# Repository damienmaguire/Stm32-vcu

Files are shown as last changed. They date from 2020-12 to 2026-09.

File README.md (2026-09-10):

# stm32-vcu (ZombieVerter VCU)

Build status

Project based on the OpenInverter System by Johannes Huebner to provide a universal VCU (Vehicle Control Unit) for electric vehicle conversion projects. 

Please visit the development thread on the Openinverter Forum for more information : https://openinverter.org/forum/viewtopic.php?f=3&t=1277
Zom_V1_3

V1.3 Hardware now released. PDFs and Gerber here on Github, full Kicad 9 design is on Patreon at the 10Eur level.

## Required Bootloader

STM32-Serial https://github.com/jsphuebner/tumanako-inverter-fw-bootloader/releases/tag/v5.2

STM32-CAN https://github.com/jsphuebner/stm32-CANBootloader

## Videos on progress

Project introduction : https://vimeo.com/506480876

V1.11a On dyno with GS450h / BMW E39 : https://vimeo.com/802405172

V2.00a now available : https://vimeo.com/824494783?share=copy

V2.15a now available : https://www.youtube.com/watch?v=iwB3wxCEFo0

V2.20A now available : https://www.youtube.com/watch?v=wjlucUWX_lc

V2.40A now available : https://vimeo.com/1201141543?fl=ip&fe=ec

# Supported components

- Nissan Leaf Gen1/2/3 inverter via CAN
- Nissan Leaf Gen1/2/3 PDM (Charger and DCDC)
- Nissan LEAF Battery (all variants)
- Mitsubishi Outlander Support
- Mitsubishi Outlander drivetrain (front and rear motors/inverters) Support
- Modular BMS / SimpBMS Support
- OpenInverter CAN Support
- CCS DC fast charge via BMW i3 LIM
- CCS DC fast charging via FOCCCI https://github.com/uhi22/ccs32clara
- Chademo DC fast charge
- ISA Shunt / BMW SBOX / VW EBOX supported via CAN
- Lexus GS450H inverter / gearbox via sync serial
- Lexus GS300H inverter / gearbox via sync serial
- Toyota Prius/Yaris/Auris Gen 3 inverters via sync serial
- BMW E46 CAN support
- BMW E39 CAN support
- BMW E65 CAN Support
- BMW E31 CAN Support
- Mid 2000s VAG Can support
- Subaru vehicle support
- Opel Ampera / Chevy Volt 6.5kw cabin heater
- VW LIN based 6.5kw cabin heater
- Elcon charger Support
- OBD2 Can support
- TESLA Gen 2 DCDC Converter Can support

# Contributing

Information on how to contribute to this open source project can be found [Contributing Guide](./CONTRIBUTING.md)

# Compiling
You will need the arm-none-eabi toolchain: https://developer.arm.com/open-source/gnu-toolchain/gnu-rm/downloads
On Linux this can be installed by typing:

`sudo apt install gcc-arm-none-eabi`

The only external depedencies are libopencm3 and libopeninv. You can download and build this dependency by typing

`make get-deps`

Now you can compile stm32-vcu by typing

`make`

# Tests

Build the tests

`make Tests`

Run the tests

`./test/test_vcu`

And upload it to your board using a JTAG/SWD adapter, the updater.py script or the esp8266 web interface

I use CodeBlocks IDE :  https://www.codeblocks.org/

Sept 21 : V1 hardware and firmware from "Master" branch now running in my E46 Touring and E39 vehicles.

March 24 : V1.1 Hardware and V2.05A firmware now running in 3 vehicles :

-BMW E39 with Lexus GS450H Drivetrain, Tesla PCS, ISA Shunt , Chademo Fast Charge

-BMW E46 Touring with Nissan Leaf Gen 1 Drivetrain, Outlander Charger / DCDC, ISA Shunt , CCS Fast Charge

-BMW E31 with Tesla LDU Drivetrain, Tesla DCDC, ISA Shunt , Chademo Fast Charge

All hardware / software is tested in these vehicles before release. More vehicles with different configuration in progress to ensure as much testing as possible.

Apr 26 : Added Zombie Relay box V1 full kicad project to hardware directory.

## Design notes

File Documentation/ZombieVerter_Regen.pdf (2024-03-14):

ZombieVerter Regen
14/03/2024
Tom dB
Pull request https://github.com/damienmaguire/Stm32-vcu/pull/78 implements regen and introduces new parameters. This document explains the new parameters.

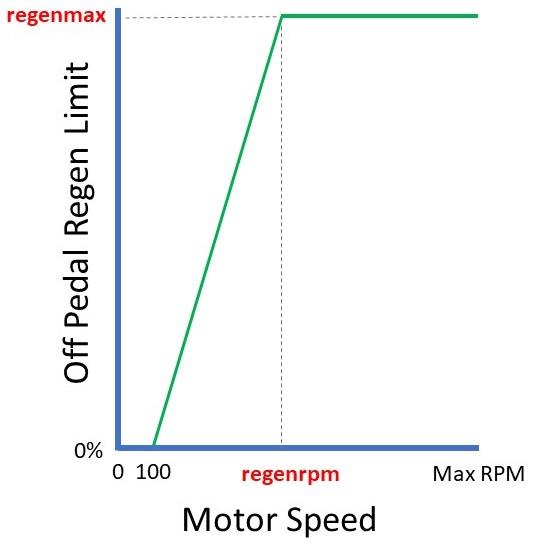
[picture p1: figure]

Regenrpm – The motor rpm at which regenmax is used as the regen limit. Under this rpm the regen limit is tapered to 0% at 100 rpm. This is applied to both Regenmax and regenBrak. Regenmax – The maximum allow regen in potnom percentage, always negative or 0. Ramps down based on motor rpm.

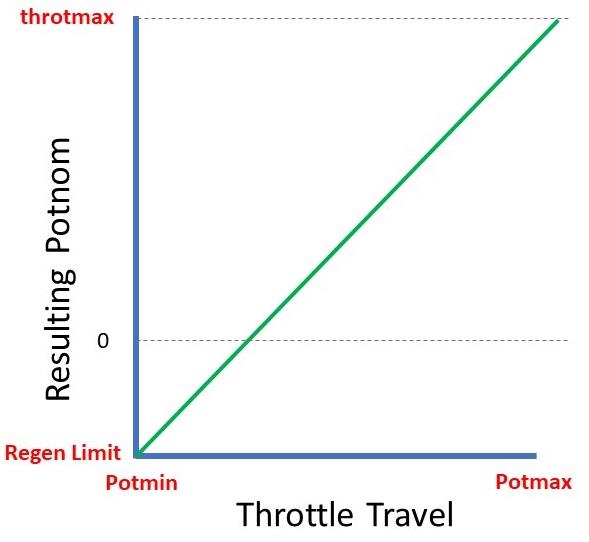
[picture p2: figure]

throtmax – Maximum allow positve potnom request in the forward direction.

throtmaxRev – Maximum allow positive potnom request in the reverse direction. Throtmin – Minimum (most negative) allowed potnom at all times.
Throtramp – The amount of allowed potnom change per %/10ms. Throtramprpm- Above this motor rpm Throtramp is no longer applied.

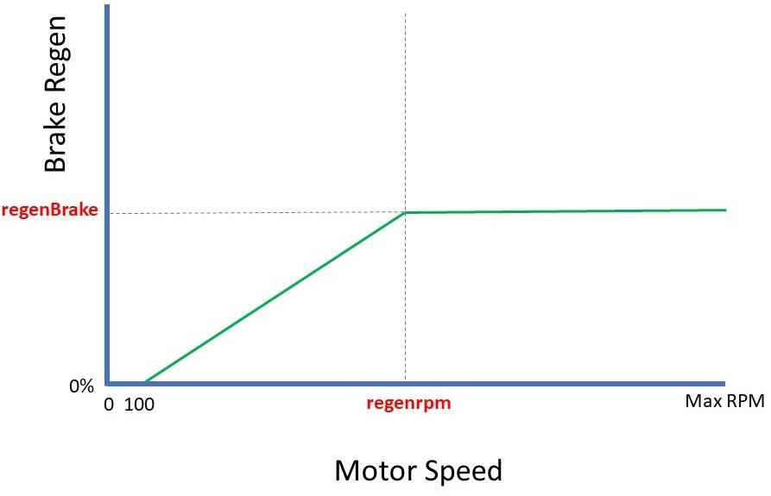
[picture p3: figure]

regenBrake – Brake pedal based negative potnom request, always negative or 0. Ramps down based on motor rpm.

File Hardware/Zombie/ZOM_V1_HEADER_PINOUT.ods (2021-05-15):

ZombieVerter VCU V1 cable side pinout.
Note: pins are referenced from the REAR of the plug.
Pin Number | Wire Colour | Function | Comment
1 | green | RS232 Rx | Rs232 comms from Usart 3 on mcu. May be used for remote wifi locating or direct serial terminal comms.
2 | purple | RS232 Tx | Rs232 comms from Usart 3 on mcu. May be used for remote wifi locating or direct serial terminal comms.
3 | white | GP Out 3 | General purpose protected Low side switched output from PD13
4 | blue | GP Out 2 | General purpose protected Low side switched output from PD14
5 | purple | PWM 3 | General purpose pwm output. Push/pull driven to +12v/gnd. Timer 3 Chan 3 PB0.
6 | orange | PWM 2 | General purpose pwm output. Push/pull driven to +12v/gnd. Timer 3 Chan 2 PA7.
7 | orange | PWM 1 | General purpose pwm output. Push/pull driven to +12v/gnd. Timer 3 Chan 1 PA6.
8 | orange | Analog 2 in | General purpose analog input 0-5v.PC3.
9 | orange | Analog 1 in | General purpose analog input 0-5v.PC2.
10 | orange | DAC 2 | Digital to Analog converter output 1. Amplified via TDA2822 to max 12v level. PA5.
11 | brown | DAC 1 | Digital to Analog converter output 1. Amplified via TDA2822 to max 12v level. PA4.
12 | blue | MG2 Temp - | Motor 2 temp sensor. Can be used for Toyota hybrid transmissions or as a general purpose motor temp input.PC4.
13 | yellow | MG2 Temp + | Motor 2 temp sensor. Can be used for Toyota hybrid transmissions or as a general purpose motor temp input.PC4.
14 | green | MG1 Temp - | Motor 2 temp sensor. Can be used for Toyota hybrid transmissions or as a general purpose motor temp input.PC5.
15 | purple | Ignition T15 In | Terminal 15 ignition on 12v input. Tells the vcu the key is in the on position.PD6.
16 | purple | REQ- | Toyota Hybrid inverter serial comms.PE6.
17 | yellow | REQ+ | Toyota Hybrid inverter serial comms.PE6.
18 | yellow | CLK- | Toyota Hybrid inverter serial comms clock. Timer 2 Channel 2. PA1.
19 | green | CLK+ | Toyota Hybrid inverter serial comms clock. Timer 2 Channel 2. PA1.
20 | green | MTH- | Toyota Hybrid inverter serial comms.Usart 2.
21 | brown | MTH+ | Toyota Hybrid inverter serial comms.Usart 2.
22 | brown | HTM- | Toyota Hybrid inverter serial comms.Usart 2.
23 | white | HTM+ | Toyota Hybrid inverter serial comms.Usart 2.
24 | green | LIN | Local interconnect network. Usart 1.
25 | blue | CAN EXT 3L | CAN 3 interface. Choice of HS/SW/FT modes via jumpers.
26 | yellow | CAN EXT 3H | CAN 3 interface. Choice of HS/SW/FT modes via jumpers.
27 | red | CAN EXT 2L | CAN 2 interface. HS only. Terminated with 120R by default.
28 | red | CAN EXT 2H | CAN 2 interface. HS only.
29 | white | MG1 Temp + | Motor 2 temp sensor. Can be used for Toyota hybrid transmissions or as a general purpose motor temp input.PC5.
30 | brown | Oil Pump PWM | PWM for Toyota hybrid oil pump speed control. Weak pullup to +12v via 1k. May be used as a general low power low side pwm output. Timer 1 channel 1 PE9.
31 | brown | GP Out 1 | General purpose protected Low side switched output from PD15.
32 | green | Inverter Power | Low side switched output for controlling drive inverter power relay.PA8.
33 | yellow | Main Contactor | Low side switched output for controlling main HV contactor.PC7.
34 | blue | Precharge | Low side switched output for controlling main HV precharge contactor.PC6.
35 | black | Pot 2 | Output from AD5160 0-5k digital potentiometer. Controlled via SPI3.
36 | purple | Pot 1 | Output from AD5160 0-5k digital potentiometer. Controlled via SPI3.
37 | green | Trans SP | Protected high side switched +12v supply to Toyota hybrid transmission. May be used as a GP output if desired.PD12.
38 | blue | Trans SL2- | Protected low side switched +12v supply to Toyota hybrid transmission. May be used as a GP output if desired.PC8.
39 | yellow | Trans SL1- | Protected low side switched +12v supply to Toyota hybrid transmission. May be used as a GP output if desired.PC9.
40 | green | Trans PB3 | Input from Toyota hybrid transmission gear position indicator. May be used as a GP input if desired.PE5.
41 | red | Trans PB2 | Input from Toyota hybrid transmission gear position indicator. May be used as a GP input if desired.PE4.
42 | black | Trans PB1 | Input from Toyota hybrid transmission gear position indicator. May be used as a GP input if desired.PE3.
43 | black | CAN EXT L | CAN 1 interface. HS only. Terminated with 120R by default.
44 | black | CAN EXT H | CAN 1 interface. HS only.
45 | black | Throttle Ground | Hall effect throttle pedal/position sensor ground.
46 | black | Throttle 2 | Hall effect throttle pedal/position sensor channel 2. PC1.
47 | black | Throttle 1 | Hall effect throttle pedal/position sensor channel 1. PC0.
48 | black | +5v Throttle | Hall effect throttle pedal/position sensor +5v supply.
49 | black | Brake input | Brake light switch input.PA15.
50 | orange | GP12v Input | General purpose 12v digital input.PD4.
51 | 2 core brown | Hvrequest | High voltage switch on/off request digital 12v input. Typically used by a charger to request HV activation.PD5.
52 | 2 core blue | Start | Start signal momentary digital 12v input. Typically connected to the start position of a traditional ignition switch.
53 | 2 core brown | Reverse Direction | Pull to +12v for reverse direction
54 | 2 core blue | Forward Direction | Pull to +12v for forward direction
55 | Purple | Ground | Connect to vehicle chassis ground
56 | Green | Permanent +12V | Connect to permanent +12v via 5amp fuse
Notes :
Yellow highlighted connections are unrouted in pre release hardware.
Workaround : Use GP analog i/p for temp and gp 12v input for brake light.
Will be corrected in release hardware.

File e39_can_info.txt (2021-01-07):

void SendBMW()
{
uint16_t outRPM = (GetInt(Param::speed)*7);
uint16_t tempValue = (GetInt(Param::tmphs)*4);
if(outRPM<4800) outRPM=4800;  //set lowest rpm to 750 displayed on tach to keep car alive thinking engine is running.
if(outRPM>44800) outRPM=44800;  //DONT READ MORE THAN 7000RPM!

 char outRPMlo = outRPM & 0xFF;
 char outRPMhi = outRPM >> 8;

char ABSMsg;
bmw dme1Data;
dme1Data.bytes[0] = 0x05;
dme1Data.bytes[1] = 0x00;
dme1Data.bytes[2] = outRPMlo;  //RPM LSB
dme1Data.bytes[3] = outRPMhi;  //RPM MSB [RPM=(hex2dec("byte3"&"byte2"))/6.4]  0x12c0 should be 750rpm on tach
dme1Data.bytes[4] = 0x00;
dme1Data.bytes[5] = 0x00;
dme1Data.bytes[6] = 0x00;
dme1Data.bytes[7] = 0x00;

    if(counter_329 >= 22) counter_329 = 0;
    if(counter_329==0) ABSMsg=0x11;
    if(counter_329>=8 && counter_329<15) ABSMsg=0x86;
    if(counter_329>=15) ABSMsg=0xd9;
    counter_329++;

bmw dme2Data;
dme2Data.bytes[0] = ABSMsg;  //needs to cycle 11,86,d9
dme2Data.bytes[1] = tempValue; //temp bit tdata
dme2Data.bytes[2] = 0xc5;
dme2Data.bytes[3] = 0x00;
dme2Data.bytes[4] = 0x00;
dme2Data.bytes[5] = 0x00; //Throttle position currently just fixed value
dme2Data.bytes[6] = 0x00;
dme2Data.bytes[7] = 0x00;

bmw dme3Data;
dme3Data.bytes[0] = 0x00;  //2=check ewwngine on , 0=check engine off
dme3Data.bytes[1] = 0x00; //LSB fuel comp
dme3Data.bytes[2] = 0x00;  //MSB fuel comp
dme3Data.bytes[3] = 0x00;   // hex 08 = Overheat light on
dme3Data.bytes[4] = 0x7E;
dme3Data.bytes[5] = 0x10;
dme3Data.bytes[6] = 0x00;
dme3Data.bytes[7] = 0x18;

 uint32_t dataBMW316[2] = {dme1Data.value[0],dme1Data.value[1] };
 uint32_t dataBMW329[2] = {dme2Data.value[0],dme2Data.value[1] };
 uint32_t dataBMW545[2] = {dme3Data.value[0],dme3Data.value[1]};

Send(0x316,dataBMW316);
Send(0x329,dataBMW329);
Send(0x545,dataBMW545);

}

 void SendBMW();

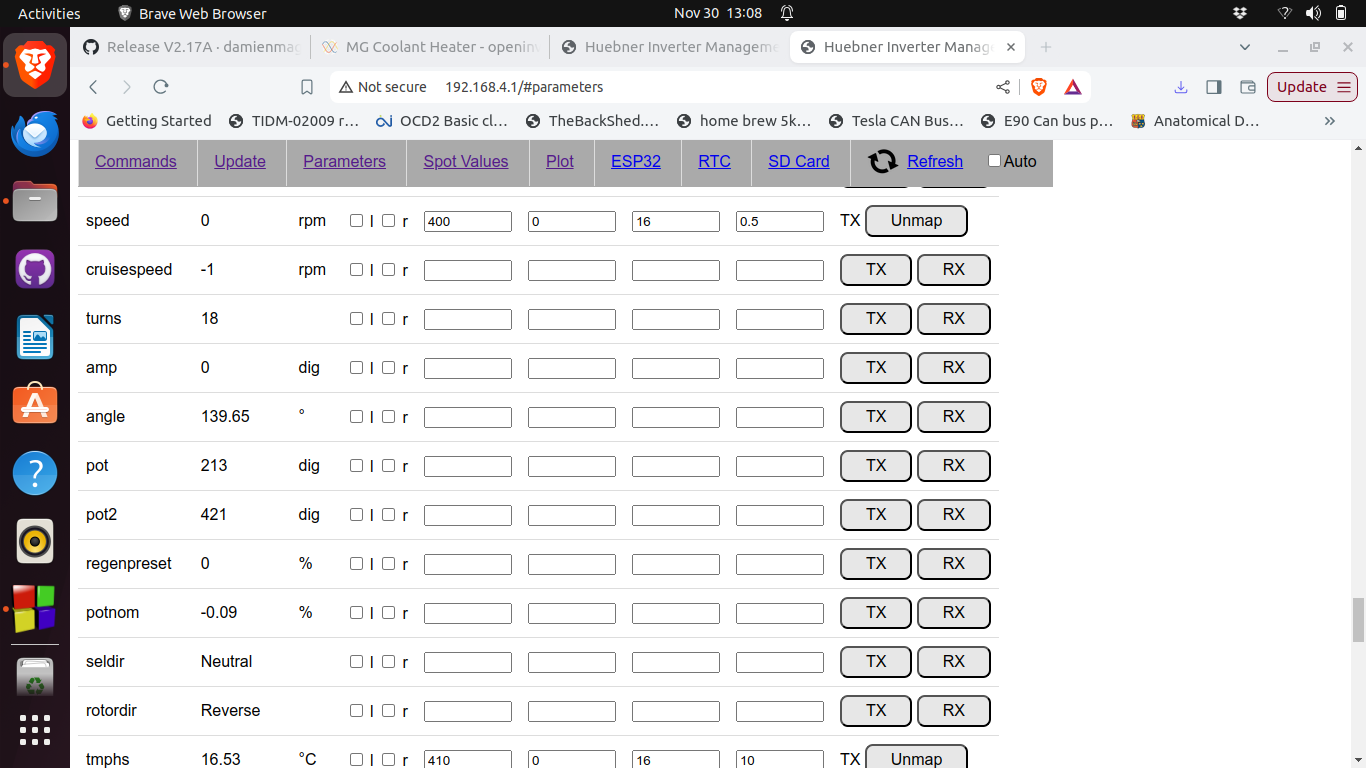
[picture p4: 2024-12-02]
Parameters/Screenshot from 2024-11-30 13-08-50.png

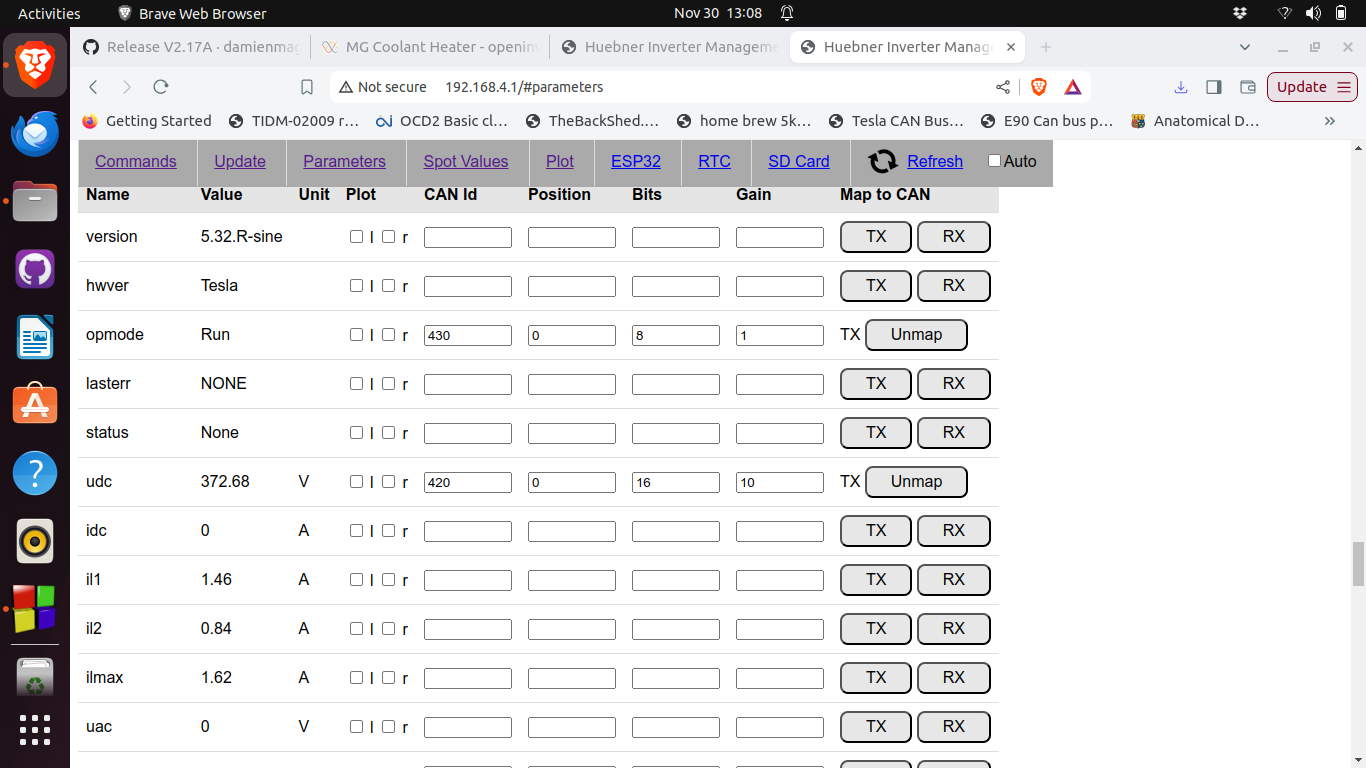
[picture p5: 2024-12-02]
Parameters/Screenshot from 2024-11-30 13-08-35.png

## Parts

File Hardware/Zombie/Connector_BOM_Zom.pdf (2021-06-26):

## ZombieVerter VCU Connector List :

### Header, Enclosure and Connector:

https://www.aliexpress.com/item/32857771975.html?spm=a2g0s.9042311.0.0.39f24c4dWOmGPE

### Wiring Harness:

https://www.aliexpress.com/item/4001213569338.html?spm=a2g0o.cart.0.0.366c3c00qhBvGO&mp=1

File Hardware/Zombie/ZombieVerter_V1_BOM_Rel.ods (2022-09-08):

Comment | Designator | Footprint
1N4148WS | D2,D3,D6,D4,D7,D8,D9,D10,D11 | SOD-323F
100uF | C17,C21 | C1206
AD5160BRJZ10-RL7 | IC21,IC22 | SOT-23-8
AMS117-3.3V | IC4
0.1uF | C4,C16,C40,C55,C34,C32,C27,C19,C43,C62,C37,C50,C51,C53,C56,C73,C74,C26,C24,C18,C28,C12,C9,C36,C41,C42 | 0805_C
0.47uF | C57,C58,C59 | 0805_C
1uF | C8,C30,C3,C2,C39,C7,C6,C5,C33,C31,C15,C44,C46,C47,C60,C61,C63,C66,C67,C70,C71,C72,C22,C14,C48,C38,C54 | 0805_C
3n3 | C45 | 0805_C
10nF | C68 | 0805_C
22pF | C10,C11 | 0805_C
100pF | C64,C65 | 0805_C
10uF | C35,C1,C49,C52,C25 | 0805_C
DLP11SA900HL2L | L4,L5 | SMD-4_1.0x1.3x0.55P
FAN3122TMX | IC27,IC28,IC29 | SOIC-8_3.9x4.9x1.27P
RED LED | LED1,LED2 | LED_0805
M24M02/M2401 | IC2 | SOIC-8_3.9x4.9x1.27P
MAX3221ECPWR | IC30 | HTSSOP-16_EP_4.4x5.0x0.65P
MCP25625T-E_ML | IC10 | QFN-28_EP_6.0x6.0x0.65P
MMBT3904 | TR1,TR2 | SOT-23-3
XL1509-5.0E1 | IC11 | SOP-8_3.9x4.9x1.27P
NCV7356D1G | IC19 | SOIC-8_3.9x4.9x1.27P
NCV8402 | IC6,IC3,IC1,IC7,IC5,IC24,IC25,IC26 | SOT-223
NCV8461DR2G | IC12 | SOIC-8_3.9x4.9x1.27P
1KΩ | R26,R25,R42,R39,R7,R17,R13,R12,R10,R9,R8,R37,R38,R30,R41,R34,R49,R55,R56,R57,R59,R60,R61,R65,R66,R23,R14 | 0805_R
1.5KΩ | R29,R6,R2,R11,R27,R51,R53 | 0805_R
1.8KΩ | R35,R43,R69 | 0805_R
2.7KΩ | R45,R46,R58,R62 | 0805_R
3KΩ | R48 | 0805_R
4.7KΩ | R28,R5,R1,R3,R4,R15,R33,R52,R54 | 0805_R
4.7Ω | R67,R68 | 0805_R
8.2KΩ | R21 | 0805
10KΩ | R18,R47,R63,R64 | 0805_R
18KΩ | R50 | 0805_R
120Ω | R44,R32,R20,R31,R24,R40,R36 | 0805_R
680Ω | R16,R22 | 0805_R
SN65HVD230QDR | IC17,IC18,IC15,IC13,IC9,IC16 | SOIC-8_3.9x4.9x1.27P
68uH | L3 | SMD-PIND-12.5x12.5x8_2.9x5.4
SS54 | D1,D5 | SMA,DO-214AC
STM32F107VCT6/GD32F107VCT6 | IC8 | LQFP-100_14.0x14.0x0.5P
100UF 6.3V | C20,C13,C23 | CASE-B_3528
TDA2822D013TR | IC23 | SOP-8_3.9x4.9x1.27P
TJA1020T_CM,118 | IC14 | SOIC-8_3.9x4.9x1.27P
TJA1055T_3_C,518 | IC20 | SOIC-14_3.9x8.7x1.27P
470uF 25V | C29,C69 | SMD-ECAP-10x10
47uH | L6 | 0805_L
MH2029-300Y | L1,L2 | 0805_L
8MHz | X1 | SMD-5032_2P
16MHZ | X2 | SMD-CRY-3225_4P
FUSE Slow Blow 500mA | F1 | 2410

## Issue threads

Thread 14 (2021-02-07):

charger.h/.cpp are missing

streber42, 2021-02-07:
Wanted to try this out and found that charger.cpp and charger.h are referenced, but missing.  Commented out for now.  Thanks for this!

damienmaguire, 2021-02-07:
Remembered to git add them this time. Should be there now.

Closed 2021-02-18.

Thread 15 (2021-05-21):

Brake input isn't connected to the MCU on the Zombieverter V1 schematic

streber42, 2021-05-21:
The pinout suggests it is PA15.

damienmaguire, 2021-05-21:
Thanks I spotted that. Will be corrected on next rev.

Closed 2022-01-06.

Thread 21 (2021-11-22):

Update codebase to include GigaDevices GD32F107 routines

JoNilsson, 2021-11-22:
At present the [GD_Zombie](https://github.com/damienmaguire/Stm32-vcu/tree/GD_Zombie) branch has fallen way behind.
Creating this issue to track status and progress of efforts to incorporate the GD32F107 back into the project and prevent it from becoming _Vaporware._

It was mentioned on the Dev forum [in this post](https://openinverter.org/forum/viewtopic.php?p=33758#p33758) that "The GD based boards will not run the firmware intended for the ST boards without the modifications that Johannes (@jsphuebner) Identified."

I suggest we start by documenting what those modification suggestions proposed by @jsphuebner on the forum were here where they belong with the code and revisioning system.

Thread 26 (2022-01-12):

brk_out and bms_in conflict with GP_analog1 and MG2_temp

streber42, 2022-01-12:
Looks like brk_out and bms_in didn't make the final design.  I'm happy to clean it up, but want to confirm they should go away and not move to a new pin.

damienmaguire, 2022-01-12:
Yeah not used in the current desigb due to limit in pins on the header. Thanks

Closed 2022-01-24.

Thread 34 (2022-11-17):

Unintended behaviour of Throttle::CalcThrottle in Single Channel Mode

crasbe, 2022-11-17:
Hello,

I suspect that the ZombieVerter might have unexpected behavior in the Single Channel Mode. This is due to the following:

The function GetUserThrottleCommand reads the analog values of throttle1 and throttle2. This is done with the anain::Get function from the libopeninv. The configuration of the anain class is _not_ conditional on the use of one or two throttle inputs:
https://github.com/damienmaguire/Stm32-vcu/blob/342305287862c44ec5a7676cfab9e281694174d6/include/anain_prj.h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

This means that in any case a value for throttle2 will be read from the GPIOs. If there's nothing connected, this must be treated as an undefined input. Probably it will be 0 because of the external pullup, but it doesn't have to be. One way or another, it should never be used in Single Channel Mode.

In the GetUserThrottleCommand function in line 80, the pot2val variable is set to Throttle::potmax[2] in Dual Channel mode, however it is not changed in Single Channel mode. This means that in Single Channel mode, the GPIO value of what was read from the GPIO (which shouldn't be used in the first place in Single Channel Mode) will be passed to CalcThrottle and most definitely be very different to Throttle::potmax[2].
In any case I'm not sure if line 80 would be a good idea anyways, since in Dual Channel mode, the pot2val variable isn't even the pot2val anymore.

utils::GetUserThrottleCommand: https://github.com/damienmaguire/Stm32-vcu/blob/ae9c2a6a5f20d4e57bed74c59c62a49651af16ca/src/utils.cpp#L49-L87

Now let's see what CalcThrottle does with the pot2val variable that's passed to it:

Throttle::CalcThrottle: https://github.com/damienmaguire/Stm32-vcu/blob/fe50dffdfaf16594421815492a9ef7a027f3e826/src/throttle.cpp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

In line 102 it checks if potmin[1] is bigger than potmax[1]. This has three issues:
1) We shouldn't use potmin[1] and potmax[1] in Single Channel Mode, because they could be set to arbitrary values.
2) pot2val is set to potmax[1] in the previous function, so the expected behavior is, that the if condition is always true.
3) It is possible however, that potmax[1] is smaller than potmin[1], if the second potentiometer is inverted to the first one. This is checked in the Throttle::CheckDualThrottle function, but not in this function.

Regarding issue 2: scaledBrkMax is set to a constant value, since pot2val was set to a constant (potmax[1]) in GetUserThrottleCommand. But this only applies in Dual Channel mode!

This will subsequently have issues on the regen behaviour.

There is a small additional bug in line 76: in case of an error with throttle 2, the error message will say throttle 1 as well.

There is a huge flaw:
https://github.com/damienmaguire/Stm32-vcu/blob/fe50dffdfaf16594421815492a9ef7a027f3e826/src/throttle.cpp#L121

regenTravel is allowed to be set to 0, so this can be a division by zero, leading to +inf on the float!

https://github.com/damienmaguire/Stm32-vcu/blob/fe50dffdfaf16594421815492a9ef7a027f3e826/src/throttle.cpp#L100
One more thing: The variable "brknompedal" is not set anywhere. This means that it's probably set to 0 (default), but it's not specified.
This means scaledBrkMax will be set to -0.1f, since potnom is multiplied by zero:
https://github.com/damienmaguire/Stm32-vcu/blob/fe50dffdfaf16594421815492a9ef7a027f3e826/src/throttle.cpp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

-------------------------

My proposed fixes are:
1) https://github.com/damienmaguire/Stm32-vcu/blob/7e766f7e7dde9166f7436f013650ff9150bd2905/include/param_prj.h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
Change POTMODE_REGENADJ to POTMODE_SINGLECHANNEL.

2) Remove the pot2val = potmax[1]; from GetUserThrottleCommand. This can not be intended behaviour.

3) Change the identity of CalcThrottle to Throttle::CalcThrottle(potval, brake). Since the plausibility of pot2val has been checked, we don't need to send it to CalcThrottle (and we shouldn't, regarding issue 1 and 3).

4) Add a range check for regenTravel to avoid uninteded behaviour (division by zero).

5) Either discard brknompedal or set it to a value.

------------------------

I will prepare a pull request, but I can't test it at the moment.

crasbe, 2022-11-17:
Small thing: "throttleRamped" in throttle.cpp is not initialized before first use.

crasbe, 2022-11-17:
As with Commit https://github.com/jsphuebner/stm32-sine/commit/8dcec8613847427cead0093dae97aabf8458d528 in the OpenInverter code, the "- 1" needs to be deleted in Lines 58 and 63:
https://github.com/damienmaguire/Stm32-vcu/blob/master/src/throttle.cpp#L51-L71

Otherwise potval can become smaller than potmin, triggering the "potnom going to infinity" issue.

jsphuebner, 2022-11-17:
Yes though this has consequences further down:
https://github.com/damienmaguire/Stm32-vcu/blob/master/src/throttle.cpp#L102
It will disable regen even when the second pot is configured to be silent. I really recommend upgrading to the latest
https://github.com/jsphuebner/stm32-sine/blob/master/src/throttle.cpp
where the behaviour has become more transparent (though to ultimate)

jsphuebner, 2022-11-17:
Also the rather large number of public member variables must be verified. They all default to 0 unless otherwise set. In the inverter ALL these variables are updated with values from parameters while the Zombie code does not explicitly set all of them

crasbe, 2022-11-17:
> Also the rather large number of public member variables must be verified. They all default to 0 unless otherwise set. In the inverter ALL these variables are updated with values from parameters while the Zombie code does not explicitly set all of them

Yes. In the OI code they are set in the main file from parameters, in the ZombieVerter code some are not set at all (like brknompedal). The Zombie doesn't even have the parameters.

https://github.com/jsphuebner/stm32-sine/blob/701875d26fdf3bfac641192990ff6174578368b6/src/stm32_sine.cpp#L302

jsphuebner, 2022-11-17:
Yes, it might not need all parameters but of course the variables must then be set to sane defaults. Might have been me who missed out on this, at least among others

crasbe, 2022-11-18:
With the pull requests #35 #36 #37 #38 this issue is fixed.

Closed 2022-11-18.

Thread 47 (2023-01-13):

Add Soft IO to Vehicle Class

Mitchy6, 2023-01-13:
To allow more flexible installations on Canbus vehicles, allow ability for Vehicle Class to send status signals replacing the DIN_Start/Fwd/Rev etc.

This method, along with the dynamic pin assignment should allow more flexibility in using CAN signals.
For the purpose of the initial update, the vehicle signal can be OR'd similar to existing canio signal.

Reason for request:
Currently the OI inverter implementation requires DigIn signals, as they are simply mapped direct to the OI CAN interface.
Attempted to replicate similar E65 type canbus shifter, however that implementation seems to duplicate and complicate things more.
Simpler solution would be to allow Vehicle Class to Mimic DigIn signals to allow similar function.
Basically at the moment there is no way to control OI other than hardwiring signals into Zombie.

In the future it will likely allow us to over-assign the DigIO supplementing with CAN based signals. and repurposing existing IO that is unused due to signals being sourced on the CAN network.

*I am aware that CANio can be possibly configured for this purpose, but the main intent is to have zombie connect to OI, while keeping the Vehicle CAN separate.

jsphuebner, 2023-01-13:
The most recent vehicle classes on the master branch already support generating the start command and direction selection

Mitchy6, 2023-01-13:
Hi Johannes, Thanks for the reply.

I've been using those within the vehicle class.
I think in that case - the issue is that the OI inverter interface should be updated to align with the gear selection/Start() that the other inverters rely on. If we're standardizing on the Gear Selection, and higher level tag statuses (Start/Cruise), we can work that to update the OI inverter message.
At the moment the OI interface is looking at the core DigIO, so it never receives the correct indication if using the higher level tags.
For a quick test, I commented out the applicable Dig_In signals from Util.cpp, and write to the applicable 'Set Param' tag in my vehicle code. This works, but for a universal solution I've been trying to find a proper way forward.
Its easy enough to re-construct the OI inverter control message based on Param::dir & Param::T15Stat, Param::cruisestt and sending it out.
I hesitated as going the Dig_IO route seemed like the more fundamental place to adjust things.

Din_Brake will remain hardwired on both Zombie and OI...

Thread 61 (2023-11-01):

Feature: Add Support for Outlander PHEV Water Header (Can controlled Version)

jamiejones85, 2023-11-01:
Details here https://openinverter.org/wiki/Mitsubishi_Outlander_Water_Heater

jamiejones85, 2023-11-24:
https://github.com/jamiejones85/Stm32-vcu/tree/OutlanderHeater Will do a PR once tested in a working vehicle.

riazarbi, 2024-02-23:
Howdy. I am motivated to test this out to get it merged to main.

I have -

1. a zombieverter
2. an outlander heater
3. a 12v water pump
4. pipes
5. wires

Any guidance as to what would constitute a valid test, @jamiejones85 ?

Tom-evnut, 2024-09-26:
@jamiejones85 Once you are happy you can heat water with the latest release please close.

jamiejones85, 2024-12-02:
Using it on my car at the moment.

Closed 2024-12-02.

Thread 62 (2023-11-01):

Improvement: Add a framework to support various Heartbeat can messages

jamiejones85, 2023-11-01:
Most HV components require a heartbeat type message, 0x285 for example with Outlander stuff. The current code setup will duplicate this message if multiple components are used.

E.G. Outlander Charger and Outlander Inverter. Both modules send out 0x285. Ideally the VCU would send this only once to each required can bus at the required intervals.

Closed 2024-12-02.

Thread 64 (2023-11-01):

Feature: Add support to stream can messages directly to SavvyCan

jamiejones85, 2023-11-01:
It would be cool to be able to stream the canbus messages to SavvyCan. This can be done with OVMS. https://github.com/openvehicles/Open-Vehicle-Monitoring-System-3/blob/master/vehicle/OVMS.V3/components/can/src/canformat_gvret.cpp

https://github.com/collin80/ESP32RET

Closed 2024-07-13.

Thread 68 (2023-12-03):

Feature: Add support for brake booster pump

jamiejones85, 2023-12-03:
Using a vacuum sensor on analogue input and a pump on digital output, when in run mode, read the input value and if under threshold (using a hysteresis value) , enable the output.

jamiejones85, 2023-12-06:
https://github.com/damienmaguire/Stm32-vcu/pull/70 PR created

jamiejones85, 2023-12-12:
Feature added with PR above

Closed 2023-12-12.

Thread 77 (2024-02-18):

Simp BMS Charge current scale factor

Manny-electric, 2024-02-18:
I am using the simp BMS option in the VCU. The BMS_ChargeLim value in the web interface seems wrong. Looking in the simpbms.cpp, the chargeCurrentLimit  is divided by 1000. The simp_BMS datasheet states that this value is scaled by 10.

7yatna, 2024-02-18:
I have noticed the same issue and didnt bother to mess with it as i really dont need this feature. but glad that you found what the issue is.

Mitchy6, 2024-10-03:
@Tom-evnut
You're likely the most active contributor. :)
Just wondering if you can roll this into an upcoming release to purge it from the issue list.

Can confirm that the scaling is currently incorrect. I've corrected it in my offline build on the bench.
If not, I'll submit a PR whenever I get my build up to date with the list of recent fixes.

Tom-evnut, 2024-10-03:
@Mitchy6 Please provide corrective lines of code and I can push this in.

chrskly, 2025-01-22:
Submitted a PR that I think will fix this.

https://github.com/damienmaguire/Stm32-vcu/pull/146

Bear in mind I don't have a ZombieVerter, so, this is just based on me eyeballing the code.

Tom-evnut, 2025-01-25:
Code merged

Closed 2025-01-25.

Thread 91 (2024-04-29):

AC Charging with Leaf PDM not functioning because 0x1D4 is not being sent in charge mode

Romukeisari, 2024-04-29:
PDM goes to fail-safe, because 1D4 is not being sent in charge mode.

Add 1D4 to PDM code, so it gets sent when in charge mode.
I have this working in my fork https://github.com/Romukeisari/Stm32-vcu-LeafLBC/blob/master/src/NissanPDM.cpp
Background: https://openinverter.org/forum/viewtopic.php?p=70232#p70232

damienmaguire, 2024-04-29:
Thanks. Will review.

Tom-evnut, 2024-05-01:
0x1D4 is sent for the inverter also, however in the STM32_vcu

This task is only called in a if function when the opmode is RUN  "402  selectedInverter->Task10Ms();"

Tom-evnut, 2024-05-01:
Create a "cleaner application" https://github.com/Tom-evnut/Stm32-vcu/tree/2.17A-Leaf-PDM-potential-fix

Romukeisari, 2024-05-07:
> Create a "cleaner application" https://github.com/Tom-evnut/Stm32-vcu/tree/2.17A-Leaf-PDM-potential-fix

If I may suggest, add a parameter read to check that also the Leaf inverter is there, otherwise this needs to be sent in all use cases so PDM doesn't go to fail-safe? Although fail-safe clears when powered off, wouldn't it be a preferred method of control to avoid the components going into fail-safe in all use cases?

Tom-evnut, 2024-05-07:
If I may suggest, add a parameter read to check that also the Leaf inverter is there

You would not use the PDM without the inverter really. Once testing is completed can review it and add it it in easily.

Tom-evnut, 2024-09-26:
@damienmaguire once you prove charging is working on your setup feel free to close this one.

Tom-evnut, 2024-12-02:
Release 2.20A fixes this, proven by @damienmaguire

Sector7e, 2024-12-27:
The update to 2.20A has fixed for my full 2013 Nissan Leaf stack with battery. I was unable to charge with version 2.17A.

Tom-evnut, 2025-01-05:
Only Gen3 PDM issues, will be its own topic.

Closed 2025-01-05.

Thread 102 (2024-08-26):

Add support for the kangoo BMS

jamiejones85, 2024-08-26:
Add the Kangoo BMS options

damienmaguire, 2024-08-27:
Okay..... :)

Tom-evnut, 2024-12-02:
Release 2.20A added this, please close

jamiejones85, 2024-12-02:
Confirmed

Closed 2024-12-02.

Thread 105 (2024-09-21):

GS450h Improvements

Tom-evnut, 2024-09-21:
I have made a new branch to do some GS450h handeling improvements.
https://github.com/Tom-evnut/Stm32-vcu/tree/GS450h-Improvements

1. MG1 does not to torque limit during shifting as its a fixed ratio - _Code in branch_
2. Do Motor blending, MG1 for driving at low throttle, until lets say 80% torque request for MG1 then bring on MG2 - _Concept Idea to be worked out_
3. Review Max torque request possible for MG1 and MG2
4. Review GS450h VCU Arduino code and compare to Zombie implementation to see any clear differences.

Closed 2025-01-05.

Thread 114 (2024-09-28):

Positive throttle in reverse direction triggers regen brake light output

SomersetEV, 2024-09-28:
When in reverse direction, positive throttle above RegenBrakeLight value triggers the brake light function.

[params Regen light in rev.json](https://github.com/user-attachments/files/17176630/params.Regen.light.in.rev.json)

SomersetEV, 2024-09-28:
Line 536 in stm32_vcu.cpp turns torquePercent negative when in reverse.
Line 550 sets BRAKELIGHT pin if torquePercent is below Param::RegenBrakeLight. In reverse torquePercent is negative, triggering the pin on acceleration instead of regen.

Tom-evnut, 2024-10-01:
https://github.com/damienmaguire/Stm32-vcu/pull/115 Pull request to fix, have not been able to test this on actual car.

Logic checks out in terms of the resulting signed value for comparison.

SomersetEV, 2024-10-30:
Testing with Outlander inverter firmware 2.20TM, no brake lights on reverse throttle but now brake lights in drive upon positive throttle. Parameters attached, from 2.17A but only Shunt parameter had to changed when updating to 2.20TM.

Reverse motor is active in this setup.

```
{
  "Inverter": 8,
  "Vehicle": 3,
  "Transmission": 0,
  "interface": 0,
  "chargemodes": 5,
  "InverterCan": 0,
  "VehicleCan": 0,
  "ShuntCan": 0,
  "LimCan": 1,
  "ChargerCan": 0,
  "BMSCan": 1,
  "OBD2Can": 1,
  "CanMapCan": 1,
  "DCDCCan": 1,
  "GearLvr": 0,
  "MotActive": 0,
  "potmin": 400,
  "potmax": 1950,
  "pot2min": 200,
  "pot2max": 970,
  "regenrpm": 1500,
  "regenendrpm": 100,
  "regenmax": -35,
  "regenBrake": -10,
  "regenramp": 1,
  "potmode": 1,
  "dirmode": 1,
  "reversemotor": 1,
  "throtramp": 10,
  "throtramprpm": 20000,
  "revlim": 9600,
  "bmslimhigh": 50,
  "bmslimlow": -1,
  "udcmin": 290,
  "udclim": 394,
  "idcmax": 5000,
  "idcmin": -5000,
  "tmphsmax": 85,
  "tmpmmax": 300,
  "throtmax": 100,
  "throtmin": -100,
  "throtmaxRev": 70,
  "throtdead": 10,
  "RegenBrakeLight": -10,
  "throtrpmfilt": 15,
  "Gear": 0,
  "OilPump": 50,
  "cruisestep": 200,
  "cruiseramp": 20,
  "regenlevel": 2,
  "udcsw": 320,
  "cruiselight": 0,
  "errlights": 0,
  "CAN3Speed": 0,
  "BattCap": 12,
  "Voltspnt": 390,
  "Pwrspnt": 3300,
  "IdcTerm": 0,
  "CCS_ICmd": 0,
  "CCS_ILim": 100,
  "CCS_SOCLim": 80,
  "SOCFC": 50,
  "Chgctrl": 0,
  "ChgAcVolt": 240,
  "ChgEff": 90,
  "DCdc_Type": 0,
  "DCSetPnt": 14,
  "BMS_Mode": 1,
  "BMS_Timeout": 10,
  "BMS_VminLimit": 3,
  "BMS_VmaxLimit": 4.12,
  "BMS_TminLimit": 0,
  "BMS_TmaxLimit": 50,
  "Heater": 0,
  "Control": 0,
  "HeatPwr": 0,
  "HeatPercnt": 0,
  "Set_Day": 0,
  "Set_Hour": 0,
  "Set_Min": 0,
  "Set_Sec": 0,
  "Chg_Hrs": 0,
  "Chg_Min": 0,
  "Chg_Dur": 0,
  "Pre_Hrs": 0,
  "Pre_Min": 0,
  "Pre_Dur": 0,
  "Out1Func": 4,
  "Out2Func": 6,
  "Out3Func": 9,
  "SL1Func": 8,
  "SL2Func": 0,
  "PWM1Func": 0,
  "PWM2Func": 0,
  "PWM3Func": 0,
  "GP12VInFunc": 0,
  "HVReqFunc": 0,
  "GPA1Func": 0,
  "GPA2Func": 0,
  "ppthresh": 2500,
  "BrkVacThresh": 2500,
  "BrkVacHyst": 2500,
  "IsaInit": 0,
  "Type": 1,
  "Tim3_Presc": 719,
  "Tim3_Period": 7200,
  "Tim3_1_OC": 3600,
  "Tim3_2_OC": 3600,
  "Tim3_3_OC": 3600
}
```

Tom-evnut, 2024-10-31:
Logic should not work motorrev. Needs verifying:
1.No motor reverse in forward yields brakelight output at right time
1.No motor reverse in reverse yields brakelight output at right time
1.Motor reverse active in forward yields brakelight output at right time
1.Motor reverse active in reverse yields brakelight output at right time

Tom-evnut, 2024-12-02:
Release 2.20A should fix this.

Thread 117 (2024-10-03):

Open-Inverter CAN control - incompatible with GearShift class

Mitchy6, 2024-10-03:
Current Open-Inverter CAN control mirror the Digi-IO signals and output direct for the external OI control.
This is incompatible with the current shifter class, whereby Gear Shifters output Drive/Neutral/Reverse (D/N/R) status.
With the increase in supported shifters, it's more likely that someone will use a shifter with OI-Inverter CAN control.

Possible solutions are to:
- Incorporate D/N/R status direct into OI-CAN logic
- OR signals to add D/N/R to CANIO within Utils.cpp
- Map D/N/R via CAN output back into itself as CANIO

Quick/Dirty solution currently is that I've added D/N/R status to CANIO portion as an additional OR signal,
However this isn't a elegant solution. and the OI-CAN logic is the only inverter to use the Digi-IO signals direct.

Best solution is to Modify OI-CAN logic for D/N/R, and let the logic in Utils.cpp convert from Digi-IO to D/N/R, thereby unifying the Inverters to all use D/N/R

PR to follow after some initial bench testing.

Tom-evnut, 2025-02-26:
To update CAN_oi to take zombie Param::dir

Tom-evnut, 2025-02-27:
Correct with https://github.com/damienmaguire/Stm32-vcu/tree/68432b9e2c54b648e5f4ae69d1ed47757c9356fa

Mapped in CanIO.cpp as it only sends Reverse and Forward as an digital on off. Both off is neutral.

Closed 2025-02-27.

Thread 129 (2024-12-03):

Open Inverter CAN control Clean up

Tom-evnut, 2024-12-03:
https://openinverter.org/forum/viewtopic.php?p=77330#p77330

1.Clean up CAN Counter
2.Clean up delayed start

Include other issue raised here: https://github.com/damienmaguire/Stm32-vcu/issues/117

Tom-evnut, 2024-12-14:
Also add mapping of OI Board CAN map to simplify configs

Tom-evnut, 2025-02-27:
Implemented https://github.com/damienmaguire/Stm32-vcu/tree/68432b9e2c54b648e5f4ae69d1ed47757c9356fa

Auto CAN Config works on bench. Waiting on bench test spins to verify controls and spot values then this can be closed.

jsphuebner, 2025-02-27:
Hi Tom,

I noticed you added SDO code to the class. Can you check whether the functions provided by cansdo.cpp can achieve the same and if not, how to tweak them to achieve what you want?
Here is an example where I use these functions: https://github.com/jsphuebner/FlyingAdcBms/blob/28bcee5f969dfb8eefe5a29063fb94b25628c799/src/bmsfsm.cpp#L121

Tom-evnut, 2025-02-27:
Hello Johannes,

Not quite sure what you mean? Are there ready made OI inter ECU CAN config functions available? It would be worth making nice clean ones.

Rewriting it to SDO commands should be possible, I will have a look tomorrow. For CAN setup we will need 3 sub indexes per message.

It is indeed something to work to getting "standardized", thanks for flagging this :)

jsphuebner, 2025-02-27:
Yes there are. I've only taken them far enough to work with the simple query in the BMS (and maybe slightly beyond). So now would be a good opportunity to flesh them out further

Tom-evnut, 2025-02-27:
Yes I already have a few ideas, I see you have the clearing of CAN maps in there which will be key.

The largest issue still is all the upfront leg work of looking up Params for ECUs and building CAN map arrays. Which is not that painful really.

Main thing I will look at is a way of standardizing stepping through each CAN map line as its 3 SDO sends.

jsphuebner, 2025-02-27:
Yes I guess even that "trilogy" could be implemented in cansdo.cpp as it's the same every time. So like sdo->SDORemoteMap(paramid, canid, position....) and so on and it then handles all the handshaking

Tom-evnut, 2025-02-27:
Yup thats my idea, I have time tomorrow to dive into this. Would make it "easier" for others to replicate or tweak.

Tom-evnut, 2025-02-28:
Im lost I cannot get it to do it right. Can you please get the CAN_OI.cpp to be able to send simple sdo requests.

Probally need to pass the canSdo instance from STM32_VCU to it some how.

Tom-evnut, 2025-02-28:
Cannot work it out how to get the SDO to propagate can you please create an example? @jsphuebner

jsphuebner, 2025-02-28:
Will look into it this week

jsphuebner, 2025-03-03:
Try this one. I haven't tested yet.
CanMap::CANPOS map;
map.offsetBits = 8;
map.length = 16;
map.gain = 0.1f;
map.offset = 0;
` sdo->RemoteMap(nodeid, rx, id, &map)`

One cycle later you can call
sdo->SDOReadReply(&dummy)
It will return true if it worked (well, or sort of worked...)
Yes you will need to pass CanSdo to the class in question

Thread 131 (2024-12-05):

Gear Change speed threshold

Tom-evnut, 2024-12-05:
Add a speed threshold under which a direction change can be requested.

Example code from OI sine

/* Only change direction when below certain motor speed and throttle is not pressed */
   if (((int)Encoder::GetSpeed() < Param::GetInt(Param::dirchrpm) || userDirSelection == rotorDir) && !potPressed)
      selectedDir = userDirSelection;

Tom-evnut, 2025-02-21:
https://github.com/damienmaguire/Stm32-vcu/pull/163

Implemented in Zombie works with all types of shifters.

Closed 2025-02-21.

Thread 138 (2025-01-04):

BrakeLight is not working

vlaarom, 2025-01-04:
Hello!

I come across one problem: BrakeLight signal low side switch is not working.

details:
Software version 2.17A
Zombieverter was manufactured using files from patreon (february 2024).
Transmission is GS450H with GS450H inverter.
This EV conversion is drivable.
I've tried to assign BrakeLight to GPOut2 and GPOut3.
I can detect din_brake (value on) when applying +12V to pin49.
On the other hand ReverseLight is working when assigned either to GPOut 2 or GPOut3.

I've attached my file with parameters
[20250104_params.json](https://github.com/user-attachments/files/18307153/20250104_params.json)

Thank you,
Vladimir

Tom-evnut, 2025-01-04:
Double posting of issue.

https://github.com/damienmaguire/Stm32-vcu/issues/114

Closed 2025-01-05.

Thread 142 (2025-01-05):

Leaf Gen3 PDM not charging

Tom-evnut, 2025-01-05:
Leaf PDM Gen3 not currently charging on release 2.20A.

Issue likely due to error state due to missing CAN comms when PDM wakes up. CAN logs collected and to be reviewed.

Tom-evnut, 2025-01-22:
Confirmed working by a forum member. https://openinverter.org/forum/viewtopic.php?p=78908#p78908

Closed 2025-01-22.

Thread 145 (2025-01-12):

TachoPPR not working with float value

Manny-electric, 2025-01-12:
currently the TachoPPR value is read as a INT

utils.cpp line 569 in void SpeedoSet(uint16_t speed)

```
float PulseGain = Param::GetInt(Param::TachoPPR);
```
should change to:

 `float PulseGain = Param::GetFloat(Param::TachoPPR);`

Tom-evnut, 2025-01-16:
Which vehicle needs a decimal pulse per revolution? Please add some info.

Most Speedos work off of ignition pulses so they would be multiples and not fractions.

Manny-electric, 2025-01-18:
I use this to drive the speedometer to show vehicle speed.  Think the code whas make to drive to tachometer, because of the 750 min and 7500 max.

But sins the variable is declared as a float and the web interface is a float. I assumed that was meant to be a float.

Tom-evnut, 2025-01-18:
Yea the web interfaces makes everything a float. I do not agree with doing that.

Yes it is to drive a tachometer. Could look at introducing an option to have it behave as a speedometer.

Proposal, new output type:
1. Start from 0
2. Float interoperation for frequency control

Sector7e, 2025-01-18:
Tom,
So the current 750 minimum is why the tach on my truck starts at 750, even though the motor isn't spinning yet. I was unable to find a way to set this to 0, so your proposal would fix my tach issue.

Tom-evnut, 2025-01-18:
Some tach signals are used to enable things like power steering ect.

Will look at adding the "speedometer" output that allows you to do a tach that shows actual rpm.

Manny-electric, 2025-01-18:
A speedo type would be good.

I have it set to start form 5 km/h. To avoid the speedo jumping at low speed. I think the timer might be loaded with more than 16 bits. could not find a clear datasheet on the timer.

The tach starting from 750 seems good to me. Can act like drive enable indicator

Tom-evnut, 2025-02-12:
Gents pull request is made https://github.com/damienmaguire/Stm32-vcu/pull/158

I bench tested this, it only work on Vehicle set to Classic

Will close once other test

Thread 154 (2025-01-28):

add pwm fuel gauge (also temp)

rstevens81, 2025-01-28:
[pwm gauge.ods](https://github.com/user-attachments/files/18576120/pwm.gauge.ods)

future request for the ability to drive fuel gauge from pwm rather than digi pots (digi pots have too high resistance in this case (e.g. 40-150 ohms)

Tom-evnut, 2025-02-12:
Added this feature https://github.com/damienmaguire/Stm32-vcu/pull/160

tested on bench by sending SOC over CAN.

Utilized a 30 ohm and 46 ohm to current limit on a mini fuel gauge

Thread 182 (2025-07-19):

Jerky torque on 450h and others

damienmaguire, 2025-07-19:
Potentially caused by compressing the throttle pedal travel into 100 steps and then mapping this to the much larger number of a drivetrain torque request. Most noticable on Toyota drivetrains with 3500 torque digits.

Tom-evnut, 2025-07-19:
Turns out there is a larger issues at hand causing some jumps in potnom

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

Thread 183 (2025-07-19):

add clutch i.e. no regen

rstevens81, 2025-07-19:
extract of my tested code...sorry forgot to merge ...

throttle.cpp

    /// cluch pedal, request no regen ... probably safest part to add this code
    bool clutch = IOMatrix::GetPin(IOMatrix::CLUTCH_NOREGEN)->Get();

    if (clutch>0)
        {
            regenlim = 0;
        }
        else
        {
            if(speed < 100 || speed <regenendRpm)//No regen under 100 rpm or speed under regenendRpm
            {
                regenlim = 0;
            }
            else if(speed < regenRpm)
            {
                regenlim = utils::change(speed, regenendRpm, regenRpm, 0, regenmax);//taper regen according to speed
            }
            else
            {
                regenlim = regenmax;
            }
        }

iomatrix.cpp
class IOMatrix
{
   public://order of these matters!
      enum pinfuncs
      {
         NONE, CHADEMOALLOW, OBCENABLE, HEATERENABLE, RUNINDICATION, WARNINDICATION,
         COOLANTPUMP, NEGCONTACTOR, BRAKELIGHT, REVERSELIGHT, HEATREQ, HVREQ,
         DCFCREQUEST, BRAKEVACPUMP, COOLINGFAN, HVACTIVE, PWM_TIM3,CP_SPOOF,
         GS450HOIL, CLUTCH_NOREGEN, LAST
      };

params_prj.h

#define PINFUNCS     "0=None, 1=ChaDeMoAlw, 2=OBCEnable, 3=HeaterEnable, 4=RunIndication, 5=WarnIndication," \
                     "6=CoolantPump, 7=NegContactor, 8=BrakeLight, 9=ReverseLight, 10=HeatReq, 11=HVRequest," \
                     "12=DCFCRequest, 13=BrakeVacPump, 14=CoolingFan, 15=HvActive, 16=PwmTim3, 17=CpSpoof,"\
                     "18=GS450pump, 19=Cluch_NoRegen"

Tom-evnut, 2025-07-19:
bool clutch = IOMatrix::GetPin(IOMatrix::CLUTCH_NOREGEN)->Get();

If the clutch is not assigned do we get returned a 0?

For heater pin we do this

```
/Reading HeatReq inpput
    if (IOMatrix::GetPin(IOMatrix::HEATREQ) != &DigIo::dummypin)//digital input has priority, check if used
    {
        Param::SetInt(Param::HeatReq,IOMatrix::GetPin(IOMatrix::HEATREQ)->Get());
    }
```

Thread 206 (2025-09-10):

Rs232 chip can't handle fastuart speeds

streber42, 2025-09-10:
**Describe the bug**
If you try to use the Rs232 chip to run a remote esp8266-web-interface it will fail to communicate.

Current steps:
1. esp8266-web-interface sends fastuart and waits for a response.
2. ZCU switches the baud rate and answers, but the the Rs232 can't handle the higher baud rate.
3. esp8266-web-interface carries on at the lower baud since it didn't get a response.
4. ZCU blindly caries on with the higher baudrate until you reset it.
5. Now it works until you reset the esp8266 again and it sends another fastuart command.

**To Reproduce**
Steps to reproduce the behavior:
1. Write up an esp8266-web-interface via the Rs232 wiring on the ZCU.

**Expected behavior**
I expect the ZCU to not switch to the faster baud rate if the Rs232 chip is in use and send something back other than "OK" to fell the esp8266-web-interface not to change the baud.  Having a param to tell it the Rs232 is in use is fine since I'm not sure how to autodetect it.

**Required Information**
Specify build: V2.00A based custom
Attach you Params: N/A but can provide if you really want

**Additional context**
I have this drafted up as another Param, but it also requires changes to libopeninv, so figured I'd go through this process to see if there is an easier fix.  I also know the ability to not run fastuart was recently removed from libopeninv, so not sure what to do about that.

Closed 2025-09-19.

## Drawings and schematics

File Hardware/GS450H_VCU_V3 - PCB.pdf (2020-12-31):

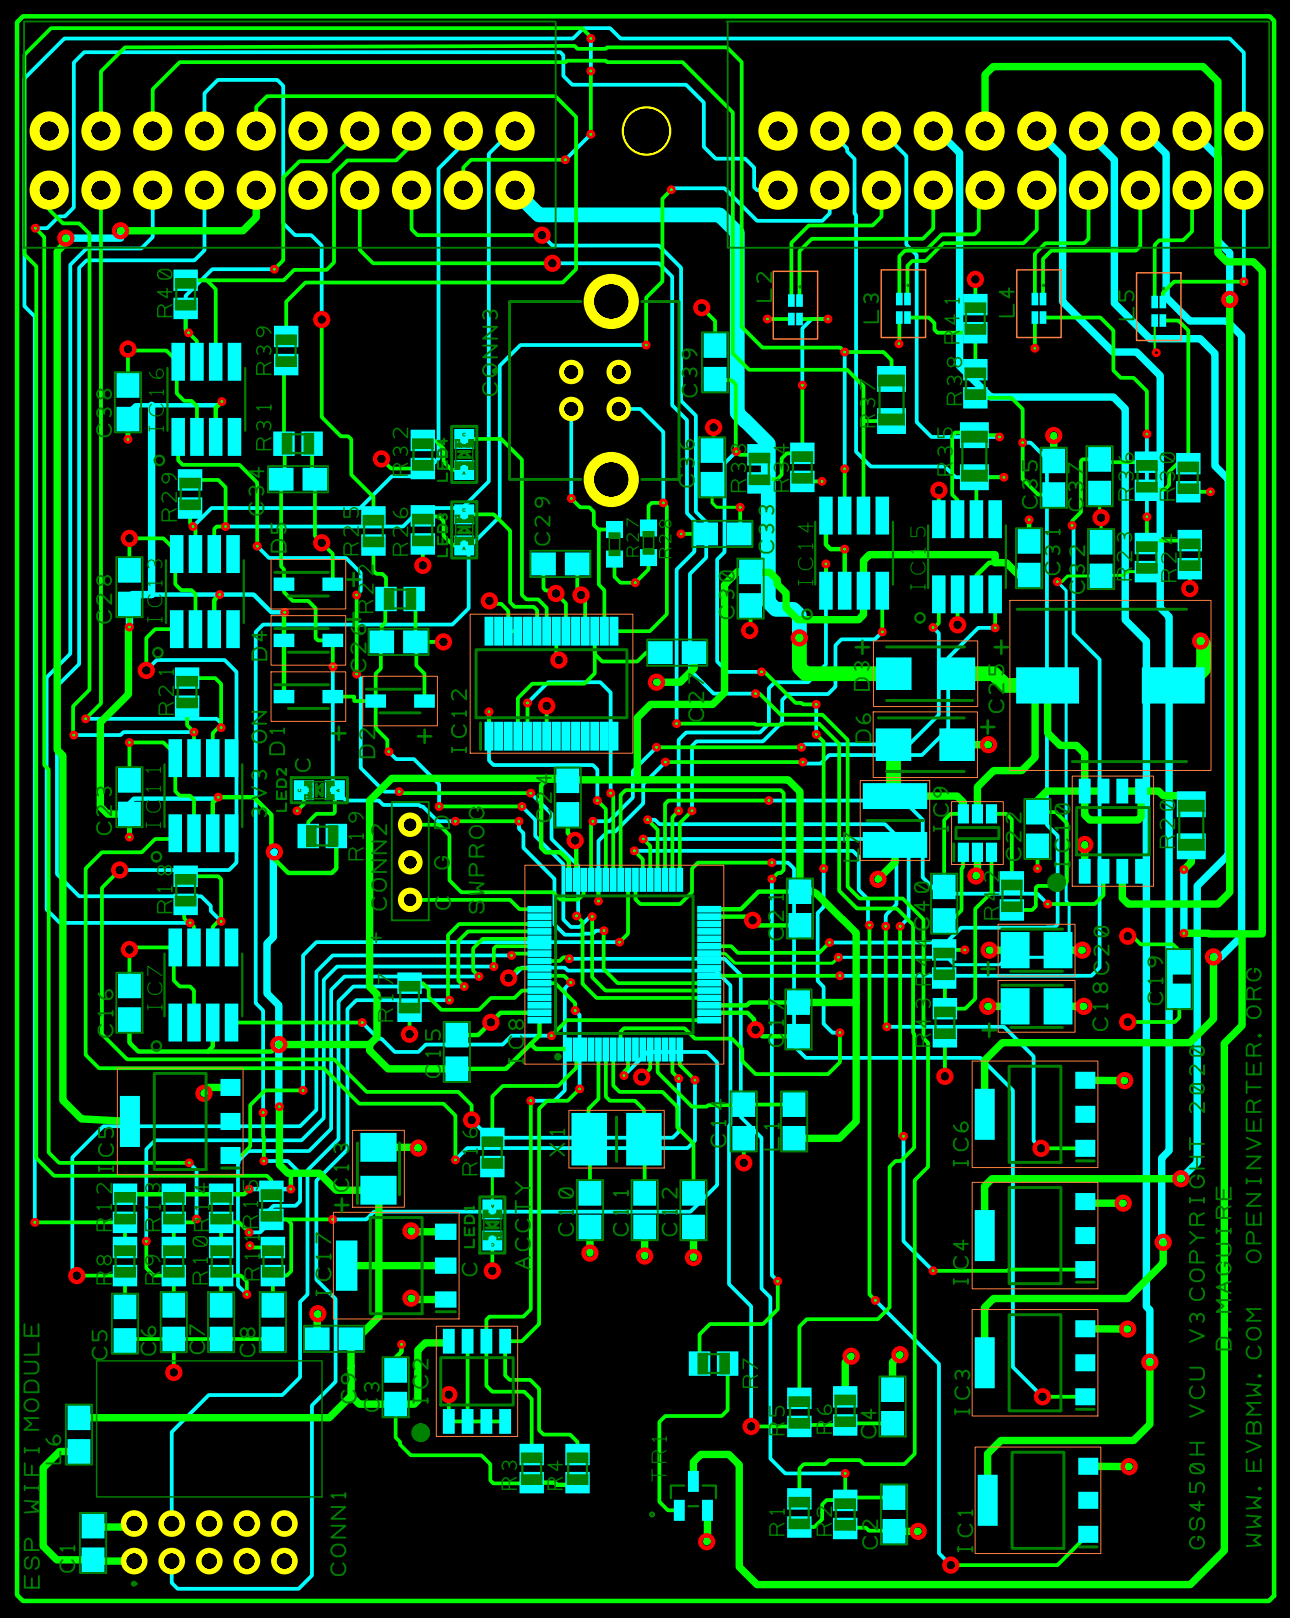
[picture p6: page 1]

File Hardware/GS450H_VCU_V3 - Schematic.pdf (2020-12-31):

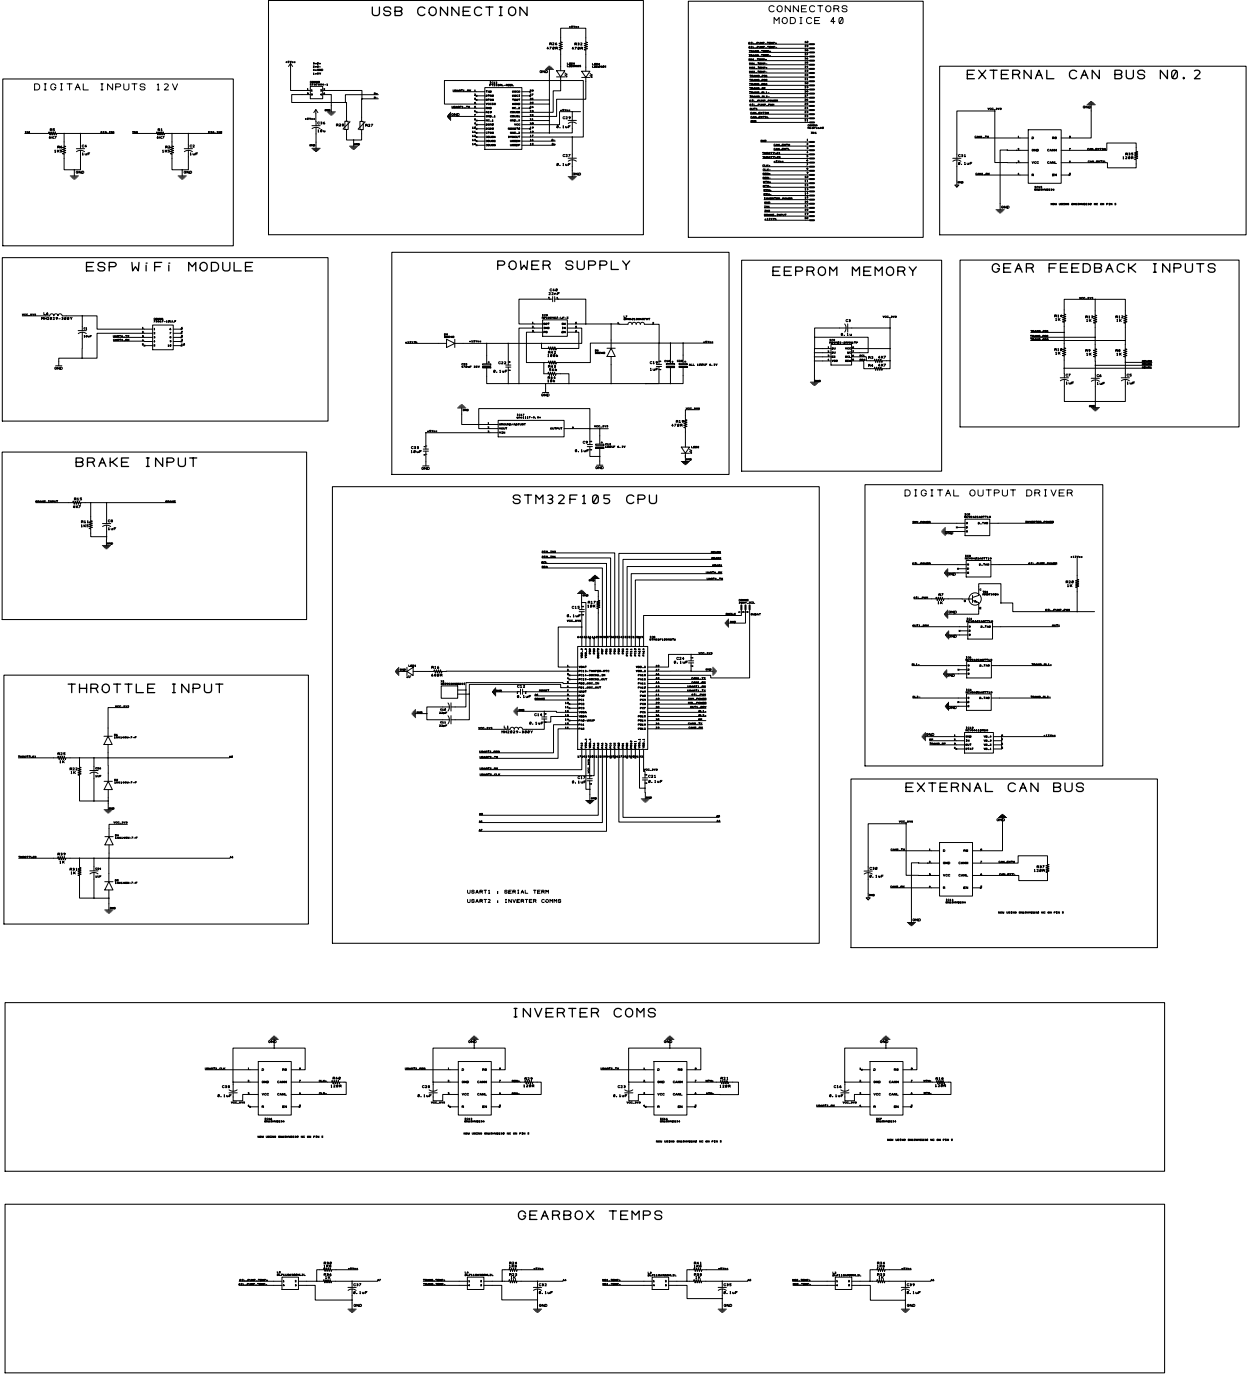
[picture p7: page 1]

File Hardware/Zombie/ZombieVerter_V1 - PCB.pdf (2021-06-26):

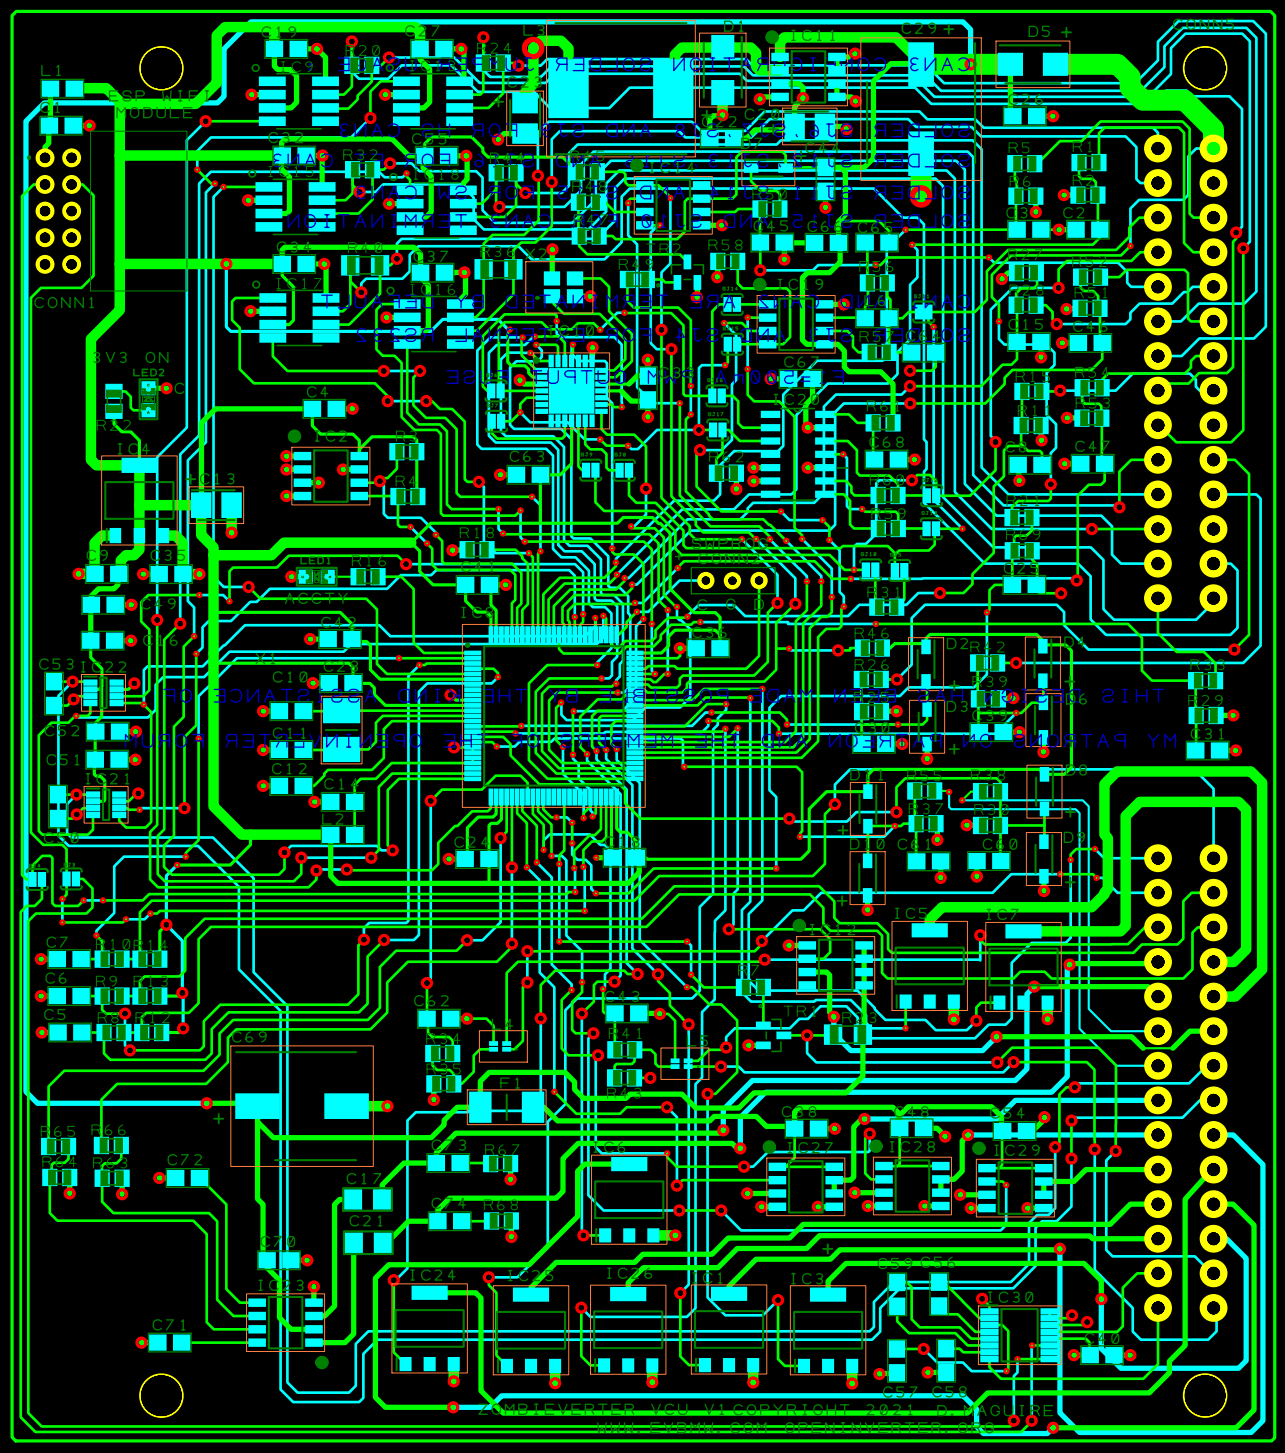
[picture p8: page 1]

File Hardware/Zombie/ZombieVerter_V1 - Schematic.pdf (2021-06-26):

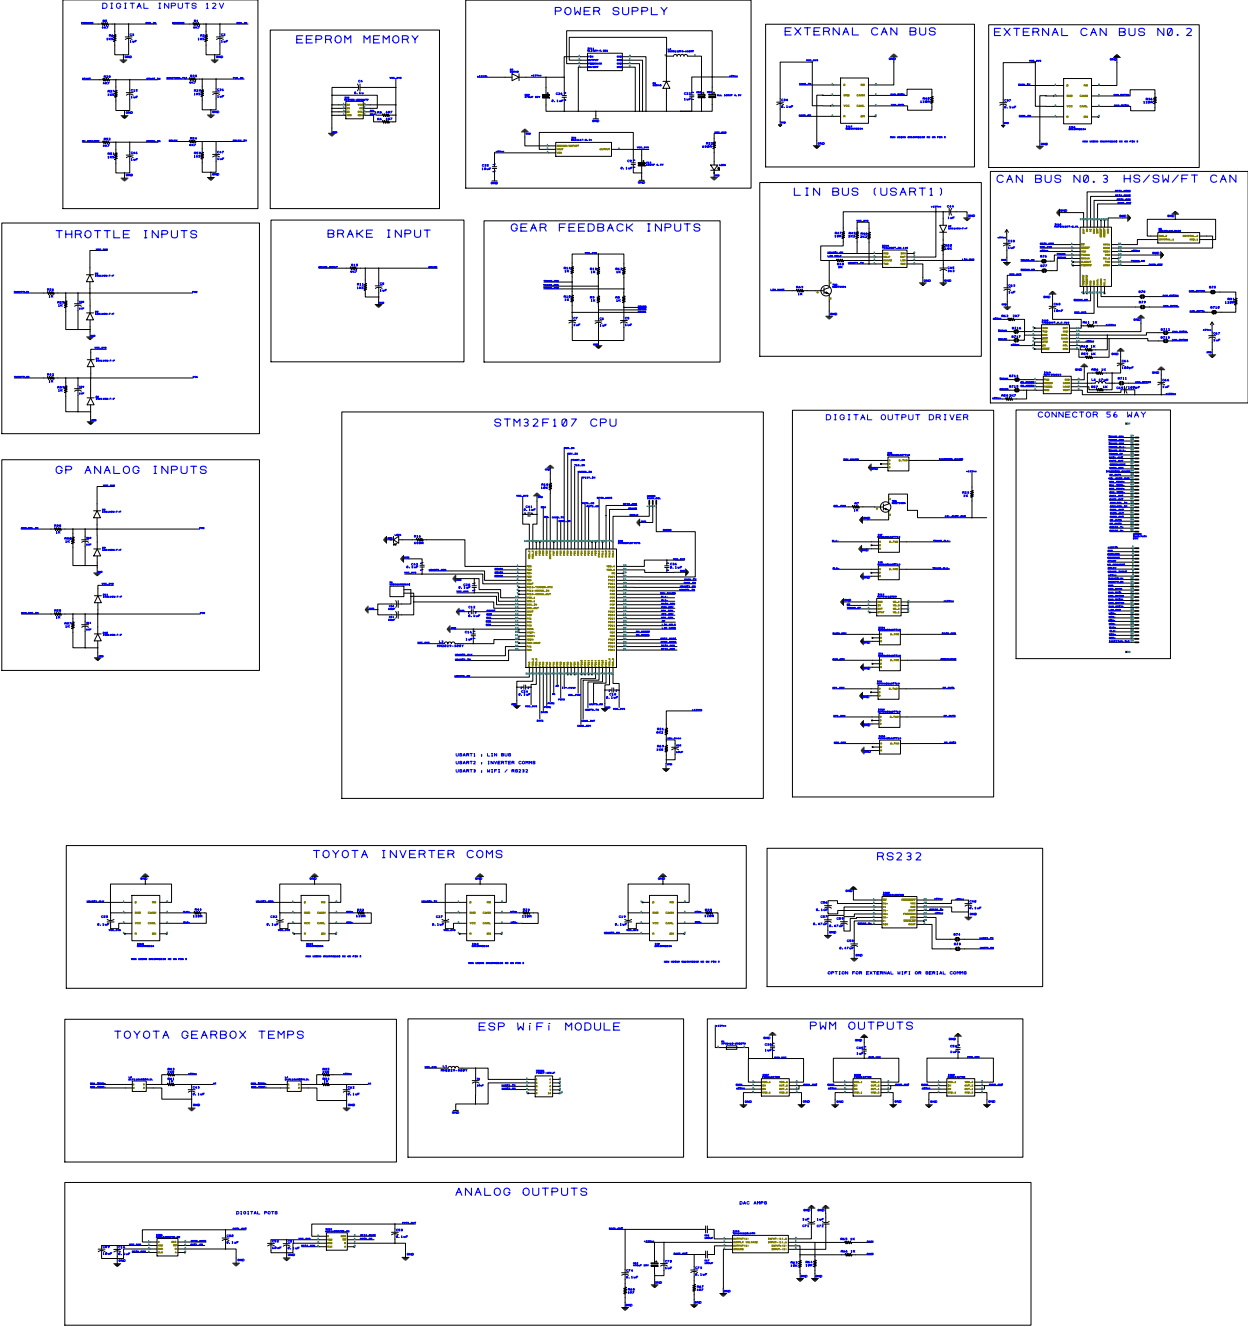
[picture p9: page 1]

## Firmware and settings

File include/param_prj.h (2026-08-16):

/*
 * This file is part of the ZombieVerter project.
 *
 * Copyright (C) 2011-2019 Johannes Huebner <dev@johanneshuebner.com>
 * Copyright (C) 2019-2022 Damien Maguire <info@evbmw.com>
 * Changes by Tom de Bree <tom@voltinflux.com> 2024
 *
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
 * You should have received a copy of the GNU General Public License
 * along with this program.  If not, see <http://www.gnu.org/licenses/>.
 */

#define VER 2.41A

/* Entries must be ordered as follows:
   1. Saveable parameters (id != 0)
   2. Temporary parameters (id = 0)
   3. Display values
 */
// Next param id (increase when adding new parameter!): 157
/*              category     name         unit       min     max     default id
 */
#define PARAM_LIST                                                             \
  PARAM_ENTRY(CAT_SETUP, Inverter, INVMODES, 0, 8, 0, 5)                       \
  PARAM_ENTRY(CAT_SETUP, Vehicle, VEHMODES, 0, 8, 0, 6)                        \
  PARAM_ENTRY(CAT_SETUP, GearLvr, SHIFTERS, 0, 4, 0, 108)                      \
  PARAM_ENTRY(CAT_SETUP, Transmission, TRNMODES, 0, 1, 0, 78)                  \
  PARAM_ENTRY(CAT_SETUP, interface, CHGINT, 0, 4, 0, 39)                       \
  PARAM_ENTRY(CAT_SETUP, chargemodes, CHGMODS, 0, 6, 0, 37)                    \
  PARAM_ENTRY(CAT_SETUP, BMS_Mode, BMSMODES, 0, 5, 0, 90)                      \
  PARAM_ENTRY(CAT_SETUP, ShuntType, SHNTYPE, 0, 4, 0, 88)                      \
  PARAM_ENTRY(CAT_SETUP, InverterCan, CAN_DEV, 0, 1, 0, 70)                    \
  PARAM_ENTRY(CAT_SETUP, VehicleCan, CAN_DEV, 0, 1, 1, 71)                     \
  PARAM_ENTRY(CAT_SETUP, ShuntCan, CAN_DEV, 0, 1, 0, 72)                       \
  PARAM_ENTRY(CAT_SETUP, LimCan, CAN_DEV, 0, 1, 0, 73)                         \
  PARAM_ENTRY(CAT_SETUP, ChargerCan, CAN_DEV, 0, 1, 1, 74)                     \
  PARAM_ENTRY(CAT_SETUP, BMSCan, CAN_DEV, 0, 1, 1, 89)                         \
  PARAM_ENTRY(CAT_SETUP, OBD2Can, CAN_DEV, 0, 1, 0, 96)                        \
  PARAM_ENTRY(CAT_SETUP, CanMapCan, CAN_DEV, 0, 1, 0, 97)                      \
  PARAM_ENTRY(CAT_SETUP, DCDCCan, CAN_DEV, 0, 1, 1, 107)                       \
  PARAM_ENTRY(CAT_SETUP, HeaterCan, CAN_DEV, 0, 1, 1, 138)                     \
  PARAM_ENTRY(CAT_SETUP, MotActive, MotorsAct, 0, 3, 0, 129)                   \
  PARAM_ENTRY(CAT_SETUP, ConfigCANOI, ONOFF, 0, 1, 0, 149)                     \
  PARAM_ENTRY(CAT_SETUP, UseRS232, ONOFF, 0, 1, 0, 155)                        \
  PARAM_ENTRY(CAT_SETUP, DriveInhibit, DRIVEINHIBITMODES, 0, 1, 0, 156)        \
  PARAM_ENTRY(CAT_THROTTLE, potmin, "dig", 0, 4095, 0, 7)                      \
  PARAM_ENTRY(CAT_THROTTLE, potmax, "dig", 0, 4095, 4095, 8)                   \
  PARAM_ENTRY(CAT_THROTTLE, pot2min, "dig", 0, 4095, 4095, 9)                  \
  PARAM_ENTRY(CAT_THROTTLE, pot2max, "dig", 0, 4095, 4095, 10)                 \
  PARAM_ENTRY(CAT_THROTTLE, regenrpm, "rpm", 100, 10000, 1500, 60)             \
  PARAM_ENTRY(CAT_THROTTLE, regenendrpm, "rpm", 100, 10000, 100, 126)          \
  PARAM_ENTRY(CAT_THROTTLE, regenmax, "%", -35, 0, -10, 61)                    \
  PARAM_ENTRY(CAT_THROTTLE, regenBrake, "%", -35, 0, -10, 122)                 \
  PARAM_ENTRY(CAT_THROTTLE, regenramp, "%/10ms", 0.1, 100, 1, 68)              \
  PARAM_ENTRY(CAT_THROTTLE, potmode, POTMODES, 0, 1, 0, 11)                    \
  PARAM_ENTRY(CAT_THROTTLE, dirmode, DIRMODES, 0, 4, 1, 12)                    \
  PARAM_ENTRY(CAT_THROTTLE, DirChange, DIRLIM, 0, 2, 0, 147)                   \
  PARAM_ENTRY(CAT_THROTTLE, DirChangeRpm, "rpm", 0, 20000, 500, 139)           \
  PARAM_ENTRY(CAT_THROTTLE, reversemotor, ONOFF, 0, 1, 0, 127)                 \
  PARAM_ENTRY(CAT_THROTTLE, throtramp, "%/10ms", 0.1, 100, 10, 13)             \
  PARAM_ENTRY(CAT_THROTTLE, throtramprpm, "rpm", 0, 20000, 20000, 14)          \
  PARAM_ENTRY(CAT_THROTTLE, revlim, "rpm", 0, 20000, 6000, 15)                 \
  PARAM_ENTRY(CAT_THROTTLE, revRegen, ONOFF, 0, 1, 0, 137)                     \
  PARAM_ENTRY(CAT_THROTTLE, udcmin, "V", 0, 1000, 450, 19)                     \
  PARAM_ENTRY(CAT_THROTTLE, udclim, "V", 0, 1000, 520, 20)                     \
  PARAM_ENTRY(CAT_THROTTLE, idcmax, "A", 0, 5000, 5000, 21)                    \
  PARAM_ENTRY(CAT_THROTTLE, idcmin, "A", -5000, 0, -5000, 22)                  \
  PARAM_ENTRY(CAT_THROTTLE, tmphsmax, "°C", 50, 150, 85, 23)                   \
  PARAM_ENTRY(CAT_THROTTLE, tmpmmax, "°C", 70, 300, 300, 24)                   \
  PARAM_ENTRY(CAT_THROTTLE, throtmax, "%", 0, 100, 100, 25)                    \
  PARAM_ENTRY(CAT_THROTTLE, throtmin, "%", -100, 0, -100, 26)                  \
  PARAM_ENTRY(CAT_THROTTLE, throtmaxRev, "%", 0, 100, 30, 123)                 \
  PARAM_ENTRY(CAT_THROTTLE, throtdead, "%", 0, 50, 10, 76)                     \
  PARAM_ENTRY(CAT_THROTTLE, RegenBrakeLight, "%", -100, 0, -15, 128)           \
  PARAM_ENTRY(CAT_THROTTLE, throtrpmfilt, "rpm/10ms", 0.1, 200, 15, 131)       \
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

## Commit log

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2021-01-08 Add .gitignore to ignore object files that have been compiled. Don't track CodeBlocks layout file. Run include/*.h through CodeBlocks AStyle plugin. Remove some blank from include/*.h. Run src/*.cpp 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
2021-01-21 E65: Update Makefile reference for BMW_E65 instead of Can_E65. E65: Rename Can_E65 to BMW_E65. E65: Move E65 global variables referenced in stm32_vcs into Class. E65: Add get and set functions for Te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
2021-01-21 Add utils namespace. Move change function into utils namespace. Move PostErrorIfRunning function into utils namespace. Move GetDigInputs function into utils namespace. Move GetUserThrottleCommand fun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
2021-01-21 GS450H: Rename class to GS450HClass. GS450H: Move 100ms task into class. GS450H: Create setTimerState function to start / stop timers for Serial data.
2021-01-23 ISA Shunt: Remove passed in id, as it is completly unused. ISA Shunt: Remove references to time. ISA Shunt: Remove milliamps variable, unused.
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2021-01-26 add v2 and v3 from isa shunt and charger mode select option
2021-01-28 fix isa shunt measurements
    [param_prj.h]
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2021-02-07 add prius gen3 menu option. disable throttle udc mapping if udcmin=0. add inverter voltage parameter.
2021-02-20 -Fix ISA voltage bugs. -Change to floats on ISA params. -Add charge mode HV control. -Add HV on/off via web interface for testing.
    [param_prj.h]
2021-02-21 -charge mode bug
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2021-05-30 Fix E46 Tach bug
    Fix E46 tach maxing ount when leaf motor runs in reverse.
    [param_prj.h]
2021-06-03 fix pilot modes more
    [param_prj.h]
2021-06-03 fix state machine return
    [param_prj.h]
2021-06-03 Fixed nested comment warning in charger.cpp
    Replace nested comments with #if 0 / #endif blocks.
    Tests:
    - Build and verify the -Wcomment warning has gone
2021-06-03 Fix state of charge calculation
    The CalcSOC() function was not being called in the
    Ms100Task though it looks like it is supposed to.
    All of the functions are now included automatically in the
    "utils" namespace in a more consistent manner to ensure
    that everthing ends up in the correct namespace and not
    accidentally in the global namespace.
    - Build and vierfy that the warning about the use of
    utils::CalcSOC has gone.
    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
2021-06-03 Temporarily suppress warning in Can_E46::Msg329()
    The temperature value supplied to Can_E46::Msg329 is not
    currently used though it probably will be in the future. Just
    mark it as unused for now so we can build without
    warnings. Hopefully this can be removed when the message
    is fixed.
    - Build and verify the warning in Can_E46.cpp is not present
    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
2021-06-03 Fix the ambiguous case with the i3LIMClass state machine
    There are several conditions which do not match specific conditions in the i3LIMClass::Control_Charge() state machine. Under these circumstances we report the No_Chg state to avoid undefined behaviour. This may not be correct.
    - Build and verify that the -Wreturn-type warning is no
    longer present in i3LIMClass::Control_Charge()
    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
2021-06-09 Change i3LIM CHG_Status from a raw value to enum
    Changing the CHG_Status to an enum should make it more
    typesafe and clearer than using a raw uint8_t and defines.
    Some unnecessary comments are removed. The old
    Status_RdyDC state has been renamed Init which seems to
    match current behaviour better.
2021-06-09 Change i3LIM CHR_Req from a raw value to enum
    Use an enum class rather than a raw value for the charge request state.
2021-06-09 Change i3LIM CHG_Ready from a raw value to enum
    Use an enum rather than a raw value for the charge ready
    state.
2021-06-09 Change i3LIM Chg_Phase from raw values to an enum
    The charge phase has a lot of different values. Make things
    clearer by changing to an enum with those values and
    remove the now duplicate comments. Use the term
    "Supoena" rather than "PreCharge" as this seems to be
    more common in the existing code. Use "Shutdown" rather
    than "Turn off" as this seems to match the comments better.
2021-06-09 Change i3LIMClass to return an enum for the charge state
    Rather than use raw hex values in the main VCU code use a
    globally accessible enum for the different charging states.
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2021-06-18 ccs status bug fix
    [param_prj.h]
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2021-07-01 i3LIM: Give contactors time to close before starting energy transfer
    During the ChargePhase::Subpoena (pre-charge) we wait
    for the contactor voltage to get within an acceptable range.
    Once this happens the contactors are requested to close.
    We should give time for the contactors to close before
    moving to the ChargePhase::EnergyTransfer.
    There is a possibility during lim_state 4 that the contactor
    voltage drifts outside the acceptable range before we close
    the contactors. If this happens reset the timer until it comes
    back inside the range.
2021-07-03 i3LIM:Proceed to Energy Transfer when contactors report closed
    Report the CCS contactor state as a read-only parameter.
    Use the change in CCS contactor state to advance out of
    Subpoena/pre-charge and into the EnergyTransfer phase
    rather than wait for a fixed period of time.
    This fixes a bug where the code would get stuck in lim_state
    == 5 because lim_stateCnt was not being incremented so
    the timer waiting for contactors to close never completed.
    - Compile tested only
    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
    [param_prj.h]
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2021-09-21 heater can fix
2021-09-21 ampera heater start bug fix
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2021-12-26 Can_E65.h defines class Can_E65 while BMW_E65.h defines class BMW_E65Class
    These two sets of files are pretty much copies of each other with stm32_vcu.cpp using BMW_E65Class from BMW_E65
    Looks like Can_E65.* is dead unused stuff?
2022-01-06 Add E46 CAN message to set Gear indicator based on the current direction.
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2022-04-15 Replaced fixed point by floating point math general cleanup
    [param_prj.h]
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2022-06-06 Add PCB BOM file
    [ZombieVerter_V1_BOM_Rel.ods]
2022-06-27 Worked on CHAdeMO, fixed crash
    [param_prj.h]
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2022-06-27 temporarily disabled ampera heater as is collided with chademo enable signal Programmed charge session teardown
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2022-08-24 Add GS300H and fix bugs
    Added GS300H to Lexus module and fix power on inv select bug.
    [param_prj.h]
2022-09-08 Update BOM with missing R14
    [ZombieVerter_V1_BOM_Rel.ods]
2022-09-09 GS450h items
    -Reinstitute gear shifts
    -Gearfeedback now from PB inputs
    -MG temp sensors calibrated.
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2022-11-14 Update Ver and 450h
    -Update the reported version to 1.01.
    -Add use of PWMs as digital op/p
    -Verify GS450h driving in vehicle
2022-11-18 Fixed the issues described in Issue #34, disabled regen for now
    [param_prj.h]
2022-11-18 Added missing bracket
2022-11-18 fixed wrong indentation of unknwon throttle mode, bumped version number, added an error message for throttle 1 and 2 fault => 12
    [param_prj.h]
2022-11-18 Bumped version number, fixed the dual throttle difference check (should not be more than 10% now), added a function to normalize the throttle input values to the [potmin, potmax] scale, added a limp 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
    [param_prj.h]
2022-11-18 Bumped version number, added throtdead parameter for a deadzone of the throttle input. This avoids torque creeping at idle.
    [param_prj.h]
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2022-11-19 Adding some tests for calc throttle to prove when brake pressed throttle is 0, regradless of if throttle pressed
2022-11-19 fix gs300h timer issue
    [param_prj.h]
2022-11-19 Added a final range check for finalSpnt
    No matter what the previous functions are doing, it should never lead to a torque request outside of the range [-100.0, 100.0].
    This could lead to wrap arounds or "funny" behavior with the inverters.
2022-11-20 fix leaf 0x11a bug
    [param_prj.h]
2022-11-21 Fix: Added 10ms inverter task call to the main 10ms task, fixing the Leaf inverter. Removed doubled defines from stm32_vcu.cpp (present in param_prj.h). Removed double check if-else for VAG. Updated 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
    [hwdefs.h, param_prj.h]
2022-11-22 Bumped version to 1.08A, changed leafinv.cpp to always send out CAN IDs 0x1DC and 0x1F2 to fix DC/DC converter behaviour. Some cosmetic changes not affecting the binary.
    [param_prj.h]
2022-11-22 Second part of Leaf DC/DC fix, call the 10ms and 100ms tasks when in run mode as well when Leaf PDM is present but not a Leaf inverter. Removed unused last_logged_final_torque_request variable.
    [param_prj.h]
2022-11-25 updates
    -fix Chademo/heater muxing
    -todo : can3 speed
    -todo : bmw auto/man
2022-12-08 CCS udates
    -Add SOCFC param to prevent stations cutting off based on soc value.
    -implement the mod from
    cschleifenbaum re Efacec cable test.
    [param_prj.h]
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2022-12-08 Fixed CAN speed enum Fixed crashes but not all yet
    [param_prj.h]
2022-12-09 Temperature fixes
    -Fix GS450H HS temp reading
    -Fix ISA temp reading
2022-12-11 Unified usage of inv_out Running RTC at 1s interval now Removed ProcessUdc() call from Ms100Task because it is also called in Ms10Task Removed some globals Moved scheduler to timer4 to be able to use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
2023-04-22 Initial BMW SBOX
    First cut at integrating the BMW SBOX contactor and measurement device as an option instead of ISA shunt.
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2023-04-26 charger mode fixes 3
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2023-04-27 heater fixes 1
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2023-04-29 current limit fix
    Fix a legacy param:get to getfloat in idc throttle limit routine. Also add as an ABS for now until regen is implemented.
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2023-05-03 lim ccs bugfix
    Fixed a lim mode bug and tested on Tritium charger 3 times to 50kw.
2023-05-04 PDM shutdown fix
    Bug fix in pdm code whereby charger would shutdown but vcu stays in charge mode until plug pulled.
2023-05-09 VW Ebox fixes
    Fixing the current reading from the Ebox. Some Johu level stuff:)
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2023-05-25 Fix a parameter id clash between ChgT and CCS_Ireq
    Found while testing an update to libopeninv
    which prevents duplicate parameter unique
    ids. Fixing this will allow correct reading of
    these values of CAN SDO with an updated
    libopeninv. As these are value parameters it
    doesn't affect saved parameters or the web
    interface.
    - Compile tested with
    https://github.com/davefiddes/libopeninv/tree/guaranteed-unique-param-ids
    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
    [param_prj.h]
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2023-08-12 Outcharger1
    First attempt at outlander charger module. this will not work:)
    [param_prj.h]
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2023-09-27 Fix Param id duplicate
    [param_prj.h]
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2023-10-29 Fix missed params updates for iomatrix_inputs change
    [param_prj.h]
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2023-11-27 Outlander Charger mods
    Can now run with no charge interface selected. Also disables 285 canbus message when not charging as that can interfere with Outlander Inverter.
2023-12-01 Fix screwups
2023-12-04 Adding Analogue inputs to IOMatrix and adding support for the Pilot Proximity on the charging port, requires threshold setting and correct resistors adding externally
    [param_prj.h]
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2023-12-22 Big bug fix
    -Fix bug causing charge mode problems in ext_digi
    -Fix call to unused charge interface
    -Fix order bug in iomatrix.
    -Change default dummy pin to a pull down.
    [param_prj.h]
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2024-02-12 Fixing issue where the vacuum pump would remain on if car turned off during pumping
2024-03-13 Throttle UDC Fix
    Fix incorrect fetch of UDC value in Throttle limit function
2024-03-14 Intial Commit
    Regen Introduction + UDC lim fix
    Also merge with https://github.com/damienmaguire/Stm32-vcu/pull/75
    [param_prj.h]
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2024-03-30 Fix Regen ramping
    Regen ramping up and down fixed.
    [param_prj.h]
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2024-04-09 fix throttle ramp
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2024-04-09 move modified .h files to correct folder
    [param_prj.h]
2024-04-10 CANOI fix
    -Fix OI startup logic
    -Update version
    [param_prj.h]
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2024-05-01 Reverse Motor Fix Outland Rear
    Clean up the serttings of reversemotor param, force zero for all except outlander rear.
    Correction for unsigned torque request number when using negatives.
    [param_prj.h]
2024-06-22 Fix punctuation of enum parameters
    There are punctuation errors in the units for the
    "Inverter", "chargemodes", "CAN3Speed" and
    "OutXFunc". The first 3 cause parse errors for the
    openinverter can tool when trying to read the
    parameter database from the device as covered in
    https://github.com/davefiddes/openinverter-can-tool/issues/4.
    Whilst this can be worked around client side it is
    better fixed in the Zombieverter.
    The issue likely causes problems with the web interface missing one or more items from the drop down.
    - Verify a fixed database is parsed correctly by OIC
    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
    [param_prj.h]
2024-07-11 Set motor speeds to 0 if comms fails, also set cruise control speed to 0 to disable it.
2024-08-07 Throttle RegenendRpm fix
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2024-08-27 Fixing build issues in master
    [param_prj.h]
2024-09-23 Initial Commit
    Add Param:
    revRegen - toggle regen on and off in reverse
    PumpPWM - Output pin function is now selectable
    FanTemp - inverter or charger temp at which Cooling fan Out goes high
    TachoPPR - Pulses per revolution for driving tachos
    Added Classic Vehicle - has tacho output and uses 12V inputs for vehicle states
    Also includes Nissan Leaf BMS framework
    Also includes tapering to limits - to be verified on vehicle
    [param_prj.h]
2024-09-24 Fix linker warning from newer toolchains
    Import commit 53afdb04 from stm32-sine which
    suppresses a linker warning:
    /usr/lib/gcc/arm-none-eabi/14.1.0/../../../../arm-none-eabi/bin/ld: warning: stm32_vcu has a LOAD segment with RWX permissions
    From the original commit:
    Due to the way that gcc generates .init_array sections
    containing C++ global object constructors it can result
    in ELF object file sections that are marked Read Write
    and eXecute. With binutils 2.39 or newer this will
    result in a warning. For an embedded use case like
    this inverter it can safely be suppressed.
    Suppressing the warning is not possible on earlier
    versions of binutils (GNU ld). The makefile now tests
    whether the l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
2024-09-24 Add Continuous Integration build using GitHub Actions
    There has been a lot of accidental build breakage with
    recent commits. To reduce the likelihood of this in
    future ensure that pushes and PRs are tested by
    running a clean build in a known clean environment
    and report any errors.
    This uses the same approach as the stm32-sine and
    ccs32clara projects for continuous integration.
    The readme is updated to display the current CI build
    state. It has also been update to reflect the changed
    build process for unit tests.
2024-09-24 Fix unit test build
    Fixing the compilation of throttle.cpp requires making utils.h suitable for cross-compilation. This is achieved by:
    - Including only the necessary .h files required to
    define types referenced in utils.h and moving all of
    the other includes to utils.cpp. It is best practice to
    do this in C/C++ to minimise dependencies. This
    requires missing includes to be added to
    BMW_E31.cpp and BMW_E39.cpp.
    - Make the utils::change() an inline header function so
    we don't need to write stubs for any STM32 specific
    code.
    The throttle now depends on params.cpp from libopeninv. This requires dummy versions of
    Param::Change() and errorListString to allow the lin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
2024-09-24 Fix unit tests by adding missing throttle default parameters
    The throttle calculation process now depends on the
    vehicle direction and maximum permitted throttle
    position being set. configure these during each test
    setup.
    - Build and run unit tests successfully
    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
2024-09-24 Fix warning in BMW_E65::GetGear
    Teh parameter outGear is currently unused so mark it
    as such to stop the compiler moaning.
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2024-09-26 Corrections for Leaf and IO Matrix
    Corrections to push correct leaf bms intergration
    IOmatrix missing update
    GS450h oilpump 0% dc fix
    [param_prj.h]
2024-09-26 Jamie Jones Merge
    -E65 updates
    -Vehicle speed
    -Warning Lights
    -Digipots for FuelLevel
    -Outlander CAN Heater
    -Heater CAN Param added
    -Outlander CAN heartbeat message implemented (shared between components)
    -Kangoo 33kWh BMS added
    -
    [param_prj.h]
2024-09-26 missing header files and ccp
    Fault on my side for doing a manual separation between WIP files and Github
    [kangoobms.h]
2024-09-26 Fix unit test build
    Reinstate the move of utils::change() to be an inline
    function similar to commit 467955d7. This allows
    utils.h to be used in both the Linux and STM32 builds.
    Currently utils.cpp is highly platform specific and
    cannot be built for Linux x86.
    - Build for STM32 and x86 Linux
    - Run unit tests on Linux successfully
    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
2024-09-27 Remove dead code from LeafBMS
    A lot of static functions and variables are defined in
    the LeafBMS class header but not implemented or
    used in the class or elsewhere in the project so can
    safely be removed.
    The exception is the LeafBMS::Temperature member
    which is assigned to during CAN decoding but never
    read from.
    Mark overridden virtual methods with "override" to
    reduce likelihood of future breakage should the
    parent method signature change.
    - Compile test only
    - Verify cppcheck reports no unexpected errors
    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
2024-09-27 Fix KangoosBMS interface
    Update the includes in kangoobms.h so that they are
    sufficient to define the KangooBMS class. Also
    update kangoobms.cpp to minimise the number of
    includes used.
    Remove the GetCurrent() method from the interface
    as there is no straightforward way for the rest of the
    project to call this and it is otherwise unused.
    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
    [kangoobms.h]
2024-09-27 Fix SimpBMS includes and interface
    No need to include all of stm32_vcu.h with dozens of
    headers. Just include the simpbms.h which has all of
    what the SimpBMS class implementation requires.
    parent method signature change
    - Build test
    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
2024-09-27 Tidy the interface and headers in DaisychainBMS
    Fix the daisychainbms.h headers to match what is
    required to define the class. Remove the catch all
    stm32_vcu.h from daisychainbms.cpp.
    Update the interface of DaisychainBMS to explicitly
    override parent methods.
    [daisychainbms.h]
2024-09-27 Remove stm32_vcu.h
    The only place that needs to use the entire list of
    headers contained in stm32_vcu.h is stm32_vcu.cpp.
    Just paste the contents in.
    The CAN3_Msg union is no longer required so can be
    safely deleted.
    - Compile test with no errors
    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
2024-09-28 correction on torque blending
2024-10-02 Fixing outlander heater bug
2024-10-30 Shutdown Delay + Jamie Merge
    -Reuse delay from contactor switching to add delay between shutting down INV Out and opening contactors.
    -Outlander Charger UDC measurement option
    -Fix GS450h Oil Pump PWM inverted
    -Added Gear option High forward Low reverse
2024-11-01 Regen Brake Light Fix
    Regen Brake Light Fix - Use potnom for comparison to simplify and fix
2024-11-04 Fix clean build due to change in libopencm3
    Commit 48d6693e pulled in an updated libopencm3
    for undocumented reasons. In principle this is a good
    idea as it fixes a nasty stack initialization bug fixed by
    @uhi22 as discussed in
    https://github.com/uhi22/ccs32clara/issues/17.
    Unfortunately the fix breaks the libopencm3 build for
    all platforms except STM32F1.
    The fix is to limit the build of libopencm3 to just the
    STM32F1 platform in the same way as the CCS32clara
    firmware.
    - Carry out a full clean build locally
    - Check GitHub CI build after push before raising a PR
    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
2024-11-13 Leaf Updates 241113
    Leaf Inv UDCinv fix, remove /2 from .h
    Leaf PDM fix, only use 0x390 for determining to start charge
    Add info on available AC current from power
    Setup to allow potential using of Spoofed CP and PP with other charge interfaces.
2024-11-19 Initial Commit
    HeatReq - if no input selected it no longer forces a state
    Input PB1 PB2 and PB3 are also now mappable. Added Inverter logic options for the pin types.
    !!!requires the latest libopeninv
    [param_prj.h]
2024-11-30 IO and Ver fix
    [param_prj.h]
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2024-12-05 Fix TorqDerate and CAN3Speed enum definitions
    The TorqDerate spot value does not display properly
    in the esp8266-web-interface. With a TorqDerate of
    13 it displays UDClimHigh. The problem is due to "+"
    being an invalid character for enum value names. As
    the field is used as a bitfield change the definition to a
    bitfield enum which the web interface can display.
    Verify behaviour with power-of-two values and mix of
    values between 0 and 31.
    Refix punctuation of CAN3Speed enum to allow it to
    be parsed by openinverter-can-tool
    [param_prj.h]
2024-12-24 IS300h FIX
    IS300h had issues of inverter comms being dead. Now resolved by removing MG1 and MG2 speed reset. Needs further investigation in the future on how to resolve comms loss.
    [param_prj.h]
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2025-01-04 Update to show correct Charge Type
2025-01-05 Mistake correct + remove new heater info
    [param_prj.h]
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2025-01-24 Update chargerint.h
    FIX for AC charging using just chargers with the "unused" "interface" selected.
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2025-01-28 fix mix up of file locations
    [param_prj.h]
2025-02-01 Fix PwmTim3 no outputting PWM
2025-02-02 Revert "Update stm32_vcu.cpp"
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2025-02-12 Added PWM Output Option SOC and Temp
    -Only in Vehicle Classic
    -Min and Max duty cycle for both, can be inverted
    -Clean up PWM prescale and period
    PWM duty is - Duty x 40 = TIM_OCx
    [param_prj.h]
2025-02-12 Update param_prj.h
    Correction of min values for DC_Max
    [param_prj.h]
2025-02-13 Outlander update + Charger Interface Clean + HVrequest
    Interface Chademo - Does not force charge on Nissan PDM, requires PDM to report Plug Present
    Outlander Charger
    - No Charge Interface, utilize PP detect to try going into charge mode
    -will enter Charge Mode for 30s: HV ON, Inv Relay ON
    -If Charger does not report CP duty above stay in Charge Mode
    -Chademo implementation -NOT WORKING with Outlander Charger
    Nissan Leaf PDM
    -Add Plug present for byte 5 being 0xn4
    STM32_VCU
    -Move running of 200ms tasks to front of 200ms main
    -Add comments about charging and logic sections
    -Set PlugDet with PP detect logic
    -Add HVrequest logic to enable HV
2025-02-27 CAN Open Inverter Update
    CAN Control of Open Inverter board update
    1.Fix sending dir instead of hardwired inputs
    2.Auto Config of Open Inverter CAN map - Added new param to activate this
    3.include DBC for this map and OI control frame
    [param_prj.h]
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2025-03-01 Move Inverter Start timer reset
    Move Inverter Start timer reset to fix starting OI board propperly
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2025-04-23 added correct DC-DC can messages
    Also added "Off" state to charger to shut down DC-DC before opening contactors
2025-04-24 dcdc fixes
    Also only sends charger shut down messages during relay delay in off mode
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2025-05-08 Correct bitshifting of Inverter voltage
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2025-05-09 Options for Heater Pot
    Added more operation modes:
    1. On Off, above or below threshold
    2. Scaling above or below threshold
    Scale HeatPercent 0-100 based on threshold and full level
    Also attempt to fix MG coolant heater staying on
    Note: sacling DOES NOTHING for most heaters right now
    [param_prj.h]
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2025-05-17 Remove throtramprpm
    throtramprpm causes major issues and will be removed until it is requested to be added back in.
    [param_prj.h]
2025-06-13 Sbox
    First Time changes made - Formatting updating
    Start up can have not ready values - fix is ignore any voltage over 600V
2025-06-14 Correction MG Gen2 Charger
    fixes to the MG Gen 2 Charger merge, no actual code changes just fixes to build
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2025-11-10 Precharge bugfix
    Fix precharge bug and confirm mg gen1 charger skeleton works
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

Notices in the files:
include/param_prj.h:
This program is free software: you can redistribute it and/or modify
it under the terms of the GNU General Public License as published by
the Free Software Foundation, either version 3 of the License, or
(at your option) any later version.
